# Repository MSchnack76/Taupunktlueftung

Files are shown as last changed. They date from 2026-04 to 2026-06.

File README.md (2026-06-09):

> [!WARNING] 
> Repository umgezogen auf die Codeberg-Plattform! Neue Versionen unter [Taupunktlueftung bei Coderberg](https://codeberg.org/MSchnack76/Taupunktlueftung.git)

# Taupunktlüftung
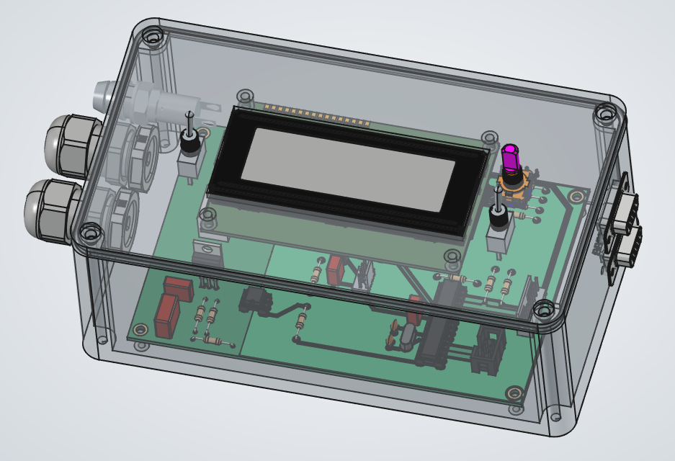
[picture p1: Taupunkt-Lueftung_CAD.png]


## Überblick
Realisierung einer Taupunkt gesteuerten Lüftung, die die Lüftung nur dann einschaltet, wenn die Taupunkt-Temperatur der Umgebungsluft (Abluftraum - bspw. außerhalb des Gebäudes) deutlich niedriger ist, als die Taupunkt-Temperatur des Raumes, der be- bzw. entlüftet werden soll.

## Elektrotechnischer Hinweis & DISCLAIMER
Ich mache an dieser Stelle darauf aufmerksam, dass diese Steuerung an einer 230V/50Hz Netzspannung betrieben wird. Es sind die einschlägigen Vorschriften für das Arbeiten, Anschließen und Betreiben einer elektrischen Anlage an 230V/50Hz zu beachten! Personen, die weder Erfahrung noch die nötige Ausbildung in der Elektrotechnik besitzen rate ich daher ausdrücklich vom Nachbau ab.
Dies ist ein Hobby-Projekt mit keinerlei Zualssung für den regelmäßigen Betrieb / Anschluss am 230V/50Hz Netz.

Alle Daten und Dateien sind nach bestem Wissen und Gewissen erstellt, haben jedoch PROTOTYPEN-Status!
Daher übernehme ich keinerlei Verantwortung für die Korrektheit der Daten und keinerlei Verantwortung für irgendwelche Schäden, die aus einem evt. Nachbau resultieren!
Diese Dokumentation ist ein rein privates Versuchs-Objekt!

## Umsetzung
### Elektronik & Leiterplatte (PCB)
Für die Steuerung kommt ein Microcontroller vom Typ Atmel 328P zum Einsatz. Der Lüfter wird über einen Optokoppler MOC3021M / TRIAC BTA 16-600 angesteuert, die mit Peripherie-Beschaltung ein Solid-State-Relais bilden.
Die Messung der Temperaturen und relativen Luftfeuchten des Abluftraumes / zu belüftenden Raumes wird über Sensoren vom Typ GY-21 HTU21 realisiert, die über einen I²C-Multiplexer TCA9543ADR an den Microcontroller angebunden werden.

Eine Daten-Ausgabe findet auf einem LCD-Display (DOT-Matrix) mit 4 Zeilen zu je 20 Zeichen (4x20) statt, welches über I²C an den Microcontroller angebunden wird. Die Hintergrundbeleuchtung des Displays kann über einen Kipptaster aktiviert werden. Der gleiche Kipptaster löst in der anderen Richtung einen Reset des Mikrocontrollers aus.

Ein Dreh-Encoder mit Tast-Funktion wird für die Menu-Steuerung eingesetzt. Das Menu und die Einstellungen werden über das LCD-Display angezeigt. Folgende Parameter können über das Menu verändert und entsprechend gesetzt werden:
a) Delta Taupunkt Schaltschwelle für das Einschalten des Lüfters (Minimales Delta zwischen Taupunkt innen und außen)
   --> Vorgabewert 5°C
b) Hystere Delta Taupunkt für das Abschalten des Lüfters
   --> Vorgabewert 1°C
c) Minimale Innenraum-Temperatur (unterhalb der Temperatur findet keine Lüftung statt)
   --> Vorgabewert 3°C
d) Minimale Außen-Temperatur (unterhalb der Temperatur findet keine Lüftung statt)
   --> Vorgabewert -10°C

Über einen Kipp-Schalter kann die Steuerung in den
1. dauerhaft EIN-Modus (Lüfter läuft ständig)
2. deaktivierten Modus (Lüfter ist dauerhaft deaktiviert)
3. in den Automatik-Modus (Taupunkt gesteuerte Be- bzw. Entlüftung)
versetzt werden.

Die Leiterplatte ist für eine Stromaufnahme von 5A bei 230VAC ausgelegt und wird über eine entsprechende Sicherung 5x20mm, 5A mittelträge vor Überstrom geschützt. Der Kleinspannungsbereich auf der PCB ist zusätzlich über eine Sicherung 5x20mm, 500mA flink abgesichert.

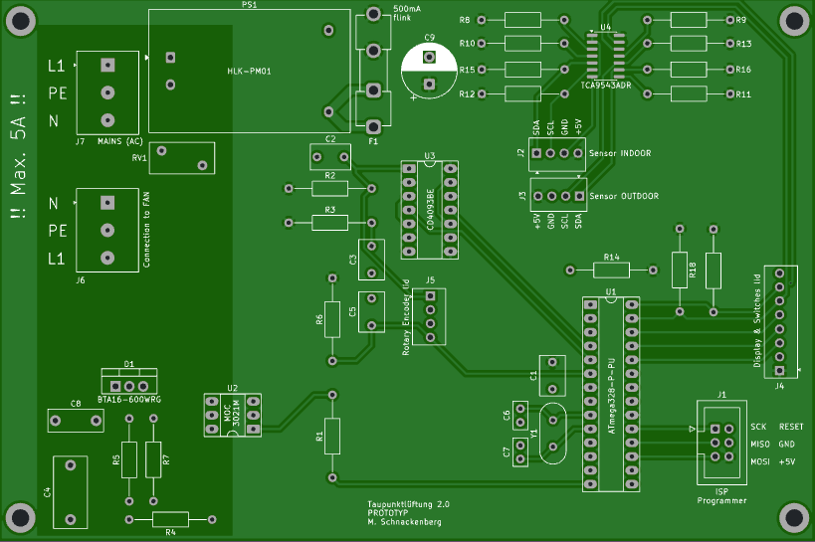
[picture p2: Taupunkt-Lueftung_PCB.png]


Der Aufbau findet bewusst im aktuellen Stadium der Entwicklung mit THT-Bauteilen (mit Ausnhame des I²C-Multiplexers, den es nur als SMD SO-14 Package gibt) statt.

### Gehäuse
Das Gehäuse wurde über eine CAD-Software konstruiert und mittels 3D-Druck erstellt. Alle Komponenten wurden im 3D-Modell eingefügt.
Die Leiterplatte sitzt auf Distanzbolzen des Gehäuses, das Display ist an der Rückseite des Deckels befestigt. Die Konnektivität der Sensoren ist über D-SUB Buchsen / Stecker realisiert.

### Verwendete Software
|Programm |Verwendung |Dateiformat |
|---|---|---|
| [FreeCAD](https://www.freecad.org) | CAD Konstruktionen | .FCStd |
| 3D-Druck | Standard Tessellation Language | .stl |
| [KiCAD](https://www.kicad.org/)| Schaltpläne | .kicad_sch |
| [KiCAD](https://www.kicad.org/)| PCB Layout | .kicad_pcb |
| [KiCAD](https://www.kicad.org/)| Projekt | .kicad_pro |
| [VisualStudioCode](https://code.visualstudio.com/)| Programmcode | .h und .cpp |
| [PlatformIO](https://platformio.org/)| Programmcode | .h und .cpp |
| [LibreOffice](https://www.libreoffice.org/)| Stückliste | .ods |

### PCB Hersteller
Ich bin sehr zufrieden mit dem deutschen PCB-Hersteller AISLER Germany GmbH mit Sitz in Aachen.

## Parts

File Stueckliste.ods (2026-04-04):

Referenz | # | Wert | Hersteller | MPN | Beschreibung
C1,C2,C3,C5 | 4 | 100n | Wima | MKS2C031001A00KSSD | MKS2 PET-Kondensator, 100 nF, 10 %, 63 VDC, RM 5
C4 | 1 | 47nF | Wima | MKP1G024703G00KSSD | 47nF 400V 10%
C6,C7 | 2 | 22p |  |  | Miniatur Scheibenkondensator, 22pF, 100V, RM 2,5mm
C8 | 1 | 10nF | Wima | MKP1G021002C00KSSD | 10nF 400V 10% Metal Film Capacitor
C9 | 1 | 1000µF/16V | Panasonic | EEUFC1C102 | Polarized capacitor 1000 µF, 16 VDC,
D1 | 1 | BTA16-600SWRG | ST | BTA16-600SWRG | TRIAC 600V 16A, TO-220AB
F1 | 1 | 500mA | ESKA | 520614 | Sicherung, 5x20mm, 500mA, flink
J1 | 1 | Wannenstecker, 6-polig, 2-reihig | Würth Electronic | 61200621621 | CONN HEADER VERT 6POS 2.54MM, 2 rows
J2, J3, J5 | 3 | Stiftleiste, 4-polig, Kodierung | binder mpe GmbH | 428-1-004-0-T-KS0 | Stiftleiste mit Kodierung und Verrastung 2,54 mm Serie 428, 4-polig
J4 | 1 | Stiftleiste, 8-polig, Kodierung | binder mpe GmbH | 428-1-008-0-T-KS0 | Stiftleiste mit Kodierung und Verrastung 2,54 mm Serie 428, 8-polig
J6, J7 | 1 | Schraubklemme, 3-polig | Metz Connect | 31073103 | Metz Connect RT026xxHBLU (Typ 073), 3-polig
J8 | 1 | Kupplungsgehäuse, 8-polig | MPE Garry GmbH | 431-1-008-X-KS0 | Kupplung, Crimptechnik, 8-polig, Leergehäuse
J9, J10, J11 | 3 | Kupplungsgehäuse, 4-polig | MPE Garry GmbH | 431-1-004-X-KS0 | Kupplung, Crimptechnik, 4-polig, Leergehäuse
 | 20 | Crimpkontakte | MPE Garry GmbH | 611-1-TX-XR | Crimpkontakte für PSK Kupplungsgehäuse
PS1 | 1 | HLK-PM01 | Shenzhen Hi-Link Electronic Co., Ltd. | HLK-PM01 | Compact AC/DC board mount power module 3W 5V
R1,R4 | 2 | 360 Ohm | YAGEO | CFR-25JT-52-360R | Kohleschicht, 360 Ohm, 5%, 250 mW, 250 VDC
R2,R3,R6 | 3 | 100 kOhm | Yageo | CFR-25JT-52-100K | Kohleschicht, 100 kOhm, 5%, 250 mW, 250 VDC
R5 | 1 | 470 Ohm | Yageo | CFR-25JT-52-470R | Kohleschicht, 470 Ohm, 5%, 250 mW, 250 VDC
R7 | 1 | 39 Ohm | VISHAY | MBB02070C3909FCT00 | 39Ω 600mW 350V Thin Film Resistor ±1%
R8,R9,R10, R11,R14 | 5 | 10k | Yageo | CFR-25JT-52-10K | Kohleschicht, 10 kOhm, 5%, 250 mW, 250 VDC
R12,R13,R15, R16,R17,R18 | 6 | 4,7 kOhm | Yageo | CFR-25JT-52-4K7 | Kohleschicht, 4,7 kOhm, 5%, 250 mW, 250 VDC
RV1 | 1 | ERZV10D391 | Panasonic | ERZV10D391 | Voltage dependent resistor 250VAC, 10%
SW1 | 1 | EC11B09 | ALPS | 401755 | Rotary encoder, dual channel, Incremental quadrate outputs, with switch
SW2 | 1 | Kippschalter, Mitte aus, 1-polig | MIYAMA | MS 500 C-B | Switch, single pole double throw, center OFF position
SW3 | 1 | Kipptaster, Mitte aus, 1-polig | MIYAMA | MS 500 E | Switch, single pole double throw, center OFF position
U1 | 1 | ATmega328-P-PU | Microchip | ATMEGA328P-PU | 20MHz, 32kB Flash, 2kB SRAM, 1kB EEPROM, DIP-28
U2 | 1 | MOC3021M | ONSEMI | MOC3021M | Random Phase Opto-Triac, Vdrm 400V, Ift 15mA, DIP6
U3 | 1 | CD4093BE | Texas Instruments | CD4093BE | CMOS Quad 2-Input NAND Schmitt Trigger
U4 | 1 | TCA9543ADR | Texas Instruments | TCA9543ADR | Low Voltage 2-Channel I2C Bus Switch
U5 | 1 | COM-LCD20X4 | Joy-IT | COM-LCD20X4 | LCD 20x4 Alphanumeric 16pin Backlight, 8bit parallel, 3.3V VDD
U6 | 1 | I2C Disp_Interface |  |  | 8-bit I/O Expander, I2C interface Module
Y1 | 1 | HC49/4H 16MHz | Würth Electronic | 830058383B | Frequenz 16,0000 MHz Frequenztoleranz 30 ppm
Sockel U1 | 1 | IC-Sockel, 28-polig | TE Connectivity | 2485264-7 | IC-Sockel, 28-polig, superflach, gedreht, schmal
Sockel U2 | 1 | IC-Sockel, 6-polig | TE Connectivity | 2485267-1 | IC-Sockel, 6-polig, superflach, gedreht, schmal
Sockel U3 | 1 | IC-Sockel, 14-polig | TE Connectivity | 2485264-2 | IC-Sockel, 14-polig, superflach, gedreht, schmal
U7, U8 | 2 | GY-21 |  |  | GY-21 Temperatur & Luftfeuchte Sensor-Modul basierend auf HTU21D
F2 | 1 | Feinsicherung 5A | ESKA | 521.024 | Sicherung, 5x20mm, 5A, mittelträge
Halter F1 | 2 | Sicherungshalter F1 | Eaton | BK/1A5601-01 | Sicherungshalter Print 5x20
Drehknopf SW1 | 1 | Kunststoffdrehknopf | CLIFF Electronic Components Ltd | CL178883 | Kunststoff-Drehknopf, schwarz, 6mm
Kappe Drehknopf SW1 | 1 | Kappe Kunststoffdrehknopf | CLIFF Electronic Components Ltd | CL1730 | Kappe für Drehknopf
J12, J13 | 2 | D-Sub 9-pol Buchse, Einbau | Encitech Connectors AB | 2101-0180-11 | D-SUB Buchse, Einbau, 9-polig, Lötkelche
J14, J15 | 2 | D-Sub 9-pol Steckverbinder | MH Connectors | MHDTZK9-DB9P-K | D-SUB Stecker, 9-polig Zweiteil. Backshell Steckverbinder
Halter F2 | 1 | Sicherungshalter F2 | SCHURTER | 3101.0015 | Sicherungshalter für 5 x 20 mm, 250 V, 10 A, schwarz
 | 1 | Leiterplatte Taupunkt-Lüftung Rev.2 | AISLER Germany GmbH |  | Leiterplatte nach Design
 | 8 | M3x10mm Selbstschneid. Schraube |  |  | Leiterplatten & Display Verschraubung
 | 4 | M4x12mm Selbstschneid. Schraube |  |  | Deckel Verschraubung auf Gehäuse
 | 4 | Distanzbolzen, 6-Kant, M3, 5mm | VOGT AG | DA5M3X05 | Verschraubung D-SUB Buchse in Gehäuse
 | 4 | Mutter, M3 |  |  | Verschraubung D-SUB Buchse in Gehäuse
 | 2 | Gegenmutter PG11 | LAPP | 53019020 | Für Zuleitungs- und Ventilator-Leitungs-Einlass
 | 2 | Verschraubung PG11 | LAPP | 53015020 | Für Zuleitungs- und Ventilator-Leitungs-Einlass
 | 1 | Gehäuse mit Deckel |  |  | nach CAD-Zeichnung, 3D-Druck
 |  | Fernmeldeleitung 2x2x0,6 |  |  | für Temperatur-Sensor-Leitung, Länge wie benötigt

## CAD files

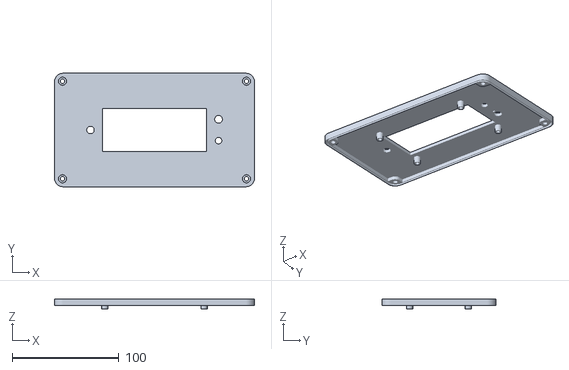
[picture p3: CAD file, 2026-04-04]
Taupunkt_Lueftung_Gehaeuse-Deckel.stl
187.4 x 106.4 x 9.00

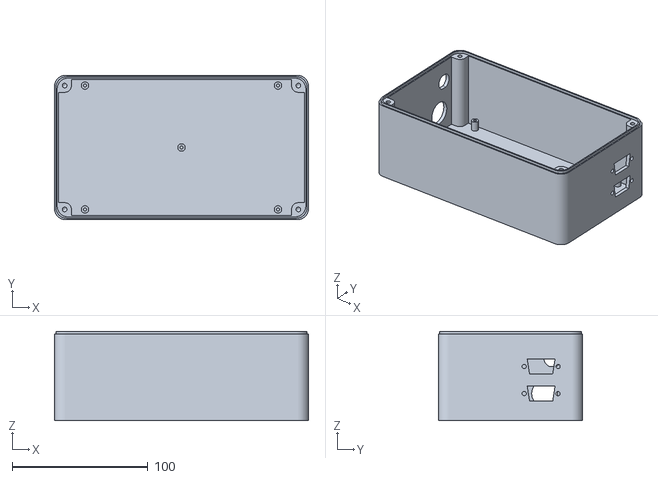
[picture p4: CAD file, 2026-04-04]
Taupunkt_Lueftung_Gehaeuse-Unterteil.stl
187.4 x 106.4 x 66.0

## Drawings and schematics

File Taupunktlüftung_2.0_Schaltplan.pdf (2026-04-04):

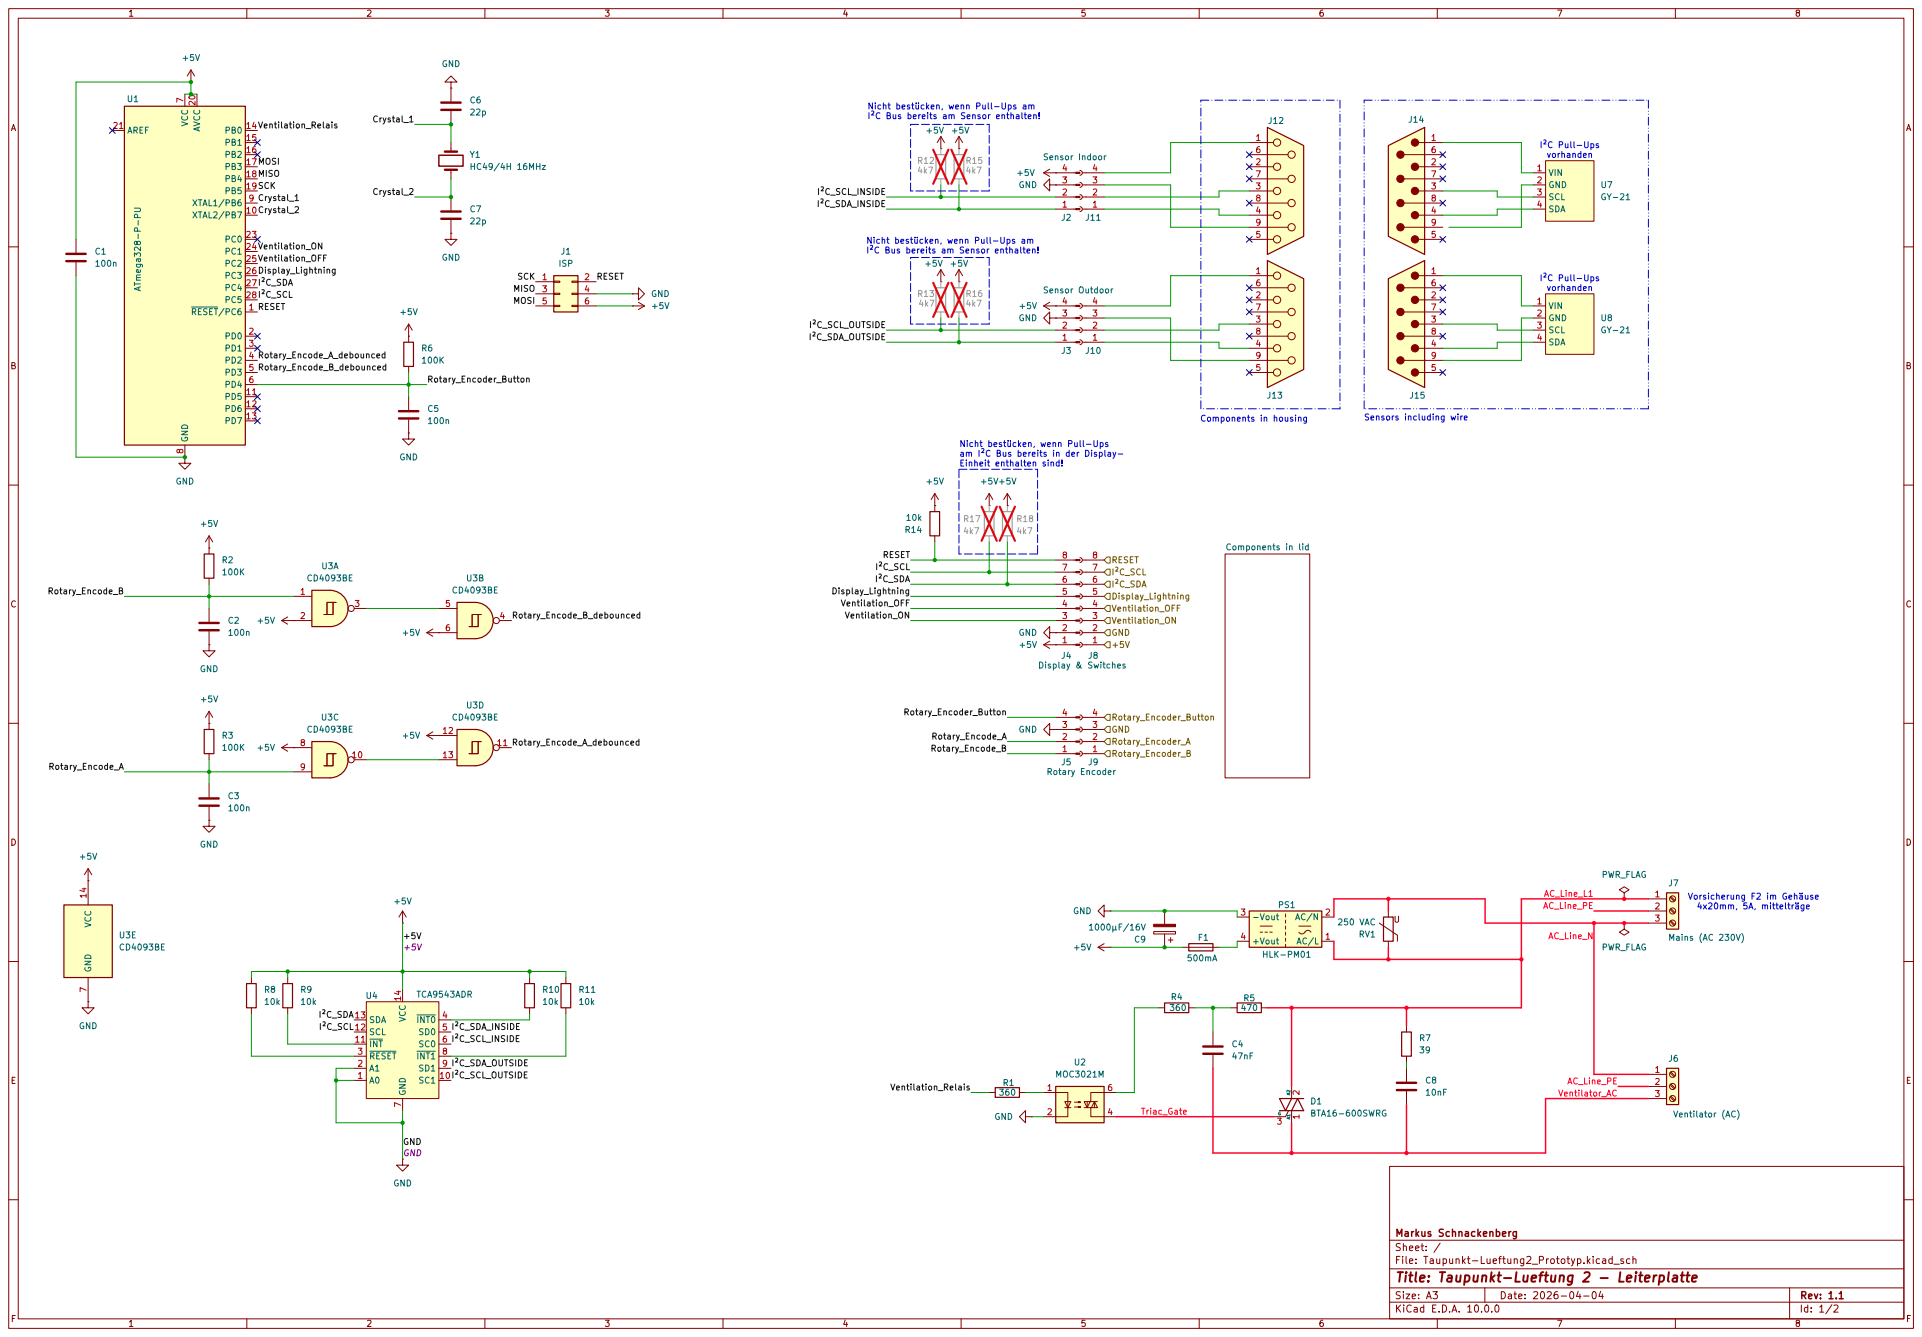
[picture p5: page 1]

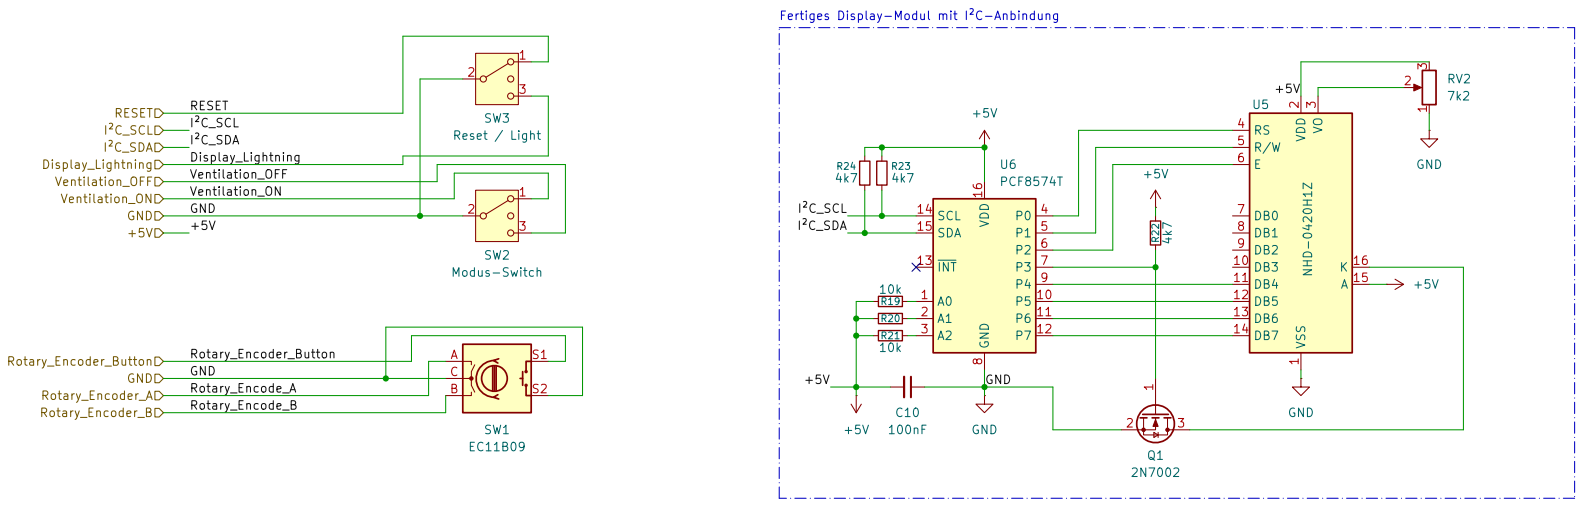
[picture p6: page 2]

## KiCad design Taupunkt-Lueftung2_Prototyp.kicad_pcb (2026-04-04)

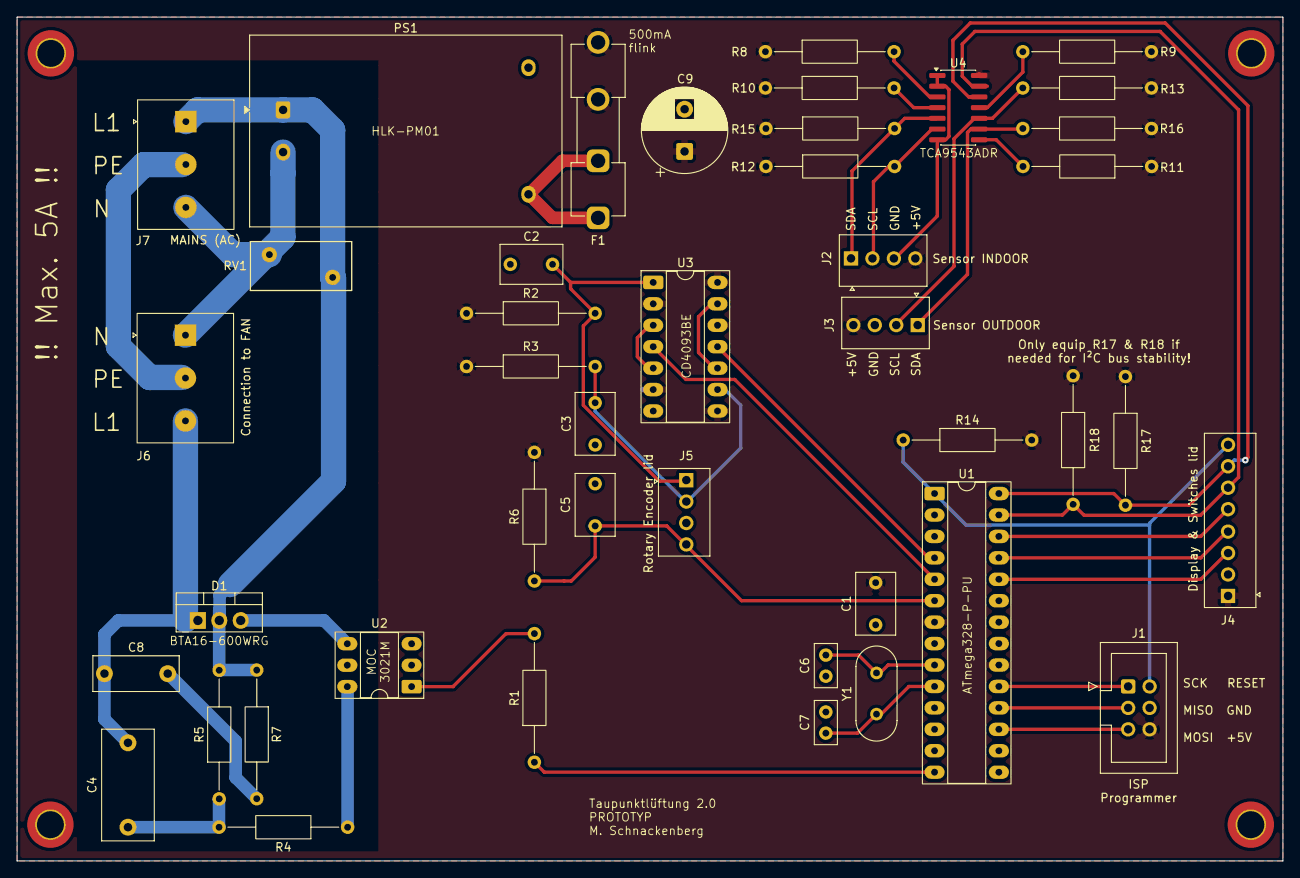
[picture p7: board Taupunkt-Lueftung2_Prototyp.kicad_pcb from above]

Board: 2 copper layers, 150.0 x 100.0 mm, 43 parts (0 on the bottom side), 39 nets.

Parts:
C1, C2, C3, C5: 100n; C_Rect_L7.2mm_W4.5mm_P5.00mm_FKS2_FKP2_MKS2_MKP2
C4: 47nF; C_Rect_L13.0mm_W6.0mm_P10.00mm_FKS3_FKP3_MKS4
C6, C7: 22p; C_Disc_D5.0mm_W2.5mm_P2.50mm
C8: 10nF; C_Rect_L10.0mm_W4.0mm_P7.50mm_FKS3_FKP3
C9: 1000µF/16V; CP_Radial_D10.0mm_P5.00mm
D1: BTA16-600SWRG; TO-220-3_Vertical
F1: 500mA; Fuseholder_Clip-5x20mm_Eaton_1A5601-01_Inline_P20.80x6.76mm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
J1: ISP; IDC-Header_2x03_P2.54mm_Vertical
J2: Sensor Indoor; Connector_Encoding_4x1_MPE_428-1-004-0-T-KS0
J3: Sensor Outdoor; Connector_Encoding_4x1_MPE_428-1-004-0-T-KS0
J4: Display & Switches; Connector_Encoding_8x1_MPE_428-1-008-0-T-KS0
J5: Rotary Encoder; Connector_Encoding_4x1_MPE_428-1-004-0-T-KS0
J6: Ventilator (AC); Connector_Screwterminal_3x1_MetzConnect_31073103
J7: Mains (AC 230V); Connector_Screwterminal_3x1_MetzConnect_31073103
PS1: HLK-PM01; Converter_ACDC_Hi-Link_HLK-PMxx
R1, R4: 360; R_Axial_DIN0207_L6.3mm_D2.5mm_P15.24mm_Horizontal
R2, R3, R6: 100K; R_Axial_DIN0207_L6.3mm_D2.5mm_P15.24mm_Horizontal
R5: 470; R_Axial_DIN0207_L6.3mm_D2.5mm_P15.24mm_Horizontal
R7: 39; R_Axial_DIN0207_L6.3mm_D2.5mm_P15.24mm_Horizontal
R8, R9, R10, R11, R14: 10k; R_Axial_DIN0207_L6.3mm_D2.5mm_P15.24mm_Horizontal
R12, R13, R15, R16, R17, R18: 4k7; R_Axial_DIN0207_L6.3mm_D2.5mm_P15.24mm_Horizontal
RV1: 250 VAC; RV_Disc_D12mm_W5.8mm_P7.5mm
U1: ATmega328-P-PU; DIP-28_W7.62mm_Socket_LongPads
U2: MOC3021M; DIP-6_W7.62mm_Socket_LongPads
U3: CD4093BE; DIP-14_W7.62mm_Socket_LongPads
U4: TCA9543ADR; SOIC-14_3.9x8.7mm_P1.27mm
Y1: HC49/4H 16MHz; Crystal_HC49-4H_Vertical

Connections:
+5V: C1.1, C9.1, F1.2, J1.6, J2.4, J3.4, J4.1, R2.1, R3.1, R6.1, R8.1, R9.1, R10.1, R11.1, R12.1, R13.1, R14.2, R15.1, R16.1, R17.1, R18.1, U1.7 (VCC), U1.20 (AVCC), U3.2, U3.6, U3.8, U3.12, U3.14 (VCC), U4.14 (VCC)
/AC_Line_L1: D1.2 (A2), J7.1, PS1.1 (AC/L), R5.2, R7.1, RV1.1
/AC_Line_N: J6.1, J7.3, PS1.2 (AC/N), RV1.2
/AC_Line_PE: J6.2, J7.2
/Crystal_1: C6.2, U1.9 (XTAL1/PB6), Y1.2
/Crystal_2: C7.1, U1.10 (XTAL2/PB7), Y1.1
/Display_Lightning: J4.5, U1.26 (PC3)
/I²C_SCL: J4.7, R17.2, U1.28 (PC5), U4.12 (SCL)
/I²C_SCL_INSIDE: J2.2, R12.2, U4.6 (SC0)
/I²C_SCL_OUTSIDE: J3.2, R13.2, U4.10 (SC1)
/I²C_SDA: J4.6, R18.2, U1.27 (PC4), U4.13 (SDA)
/I²C_SDA_INSIDE: J2.1, R15.2, U4.5 (SD0)
/I²C_SDA_OUTSIDE: J3.1, R16.2, U4.9 (SD1)
/MISO: J1.3, U1.18 (PB4)
/MOSI: J1.5, U1.17 (PB3)
/RESET: J1.2, J4.8, R14.1, U1.1 (~RESET/PC6)
/Rotary_Encode_A: C3.1, J5.2, R3.2, U3.9
/Rotary_Encode_A_debounced: U1.4 (PD2), U3.11
/Rotary_Encode_B: C2.1, J5.1, R2.2, U3.1
/Rotary_Encode_B_debounced: U1.5 (PD3), U3.4
/Rotary_Encoder_Button: C5.1, J5.4, R6.2, U1.6 (PD4)
/SCK: J1.1, U1.19 (PB5)
/Triac_Gate: D1.3 (G), U2.4
/Ventilation_OFF: J4.4, U1.25 (PC2)
/Ventilation_ON: J4.3, U1.24 (PC1)
/Ventilation_Relais: R1.1, U1.14 (PB0)
/Ventilator_AC: C4.2, C8.2, D1.1 (A1), J6.3
GND: C1.2, C2.2, C3.2, C5.2, C6.1, C7.2, C9.2, J1.4, J2.3, J3.3, J4.2, J5.3, PS1.3 (-Vout), U1.8 (GND), U1.22 (GND), U2.2, U3.7 (GND), U4.1 (A0), U4.2 (A1), U4.7 (GND)
unnamed: C4.1, R4.2, R5.1
unnamed: C8.1, R7.2
unnamed: F1.1, PS1.4 (+Vout)
unnamed: R1.2, U2.1
unnamed: R4.1, U2.6
unnamed: U3.3, U3.5
unnamed: U3.10, U3.13
unnamed: R10.2, U4.4 (~INT0)
unnamed: R11.2, U4.8 (~INT1)
unnamed: R9.2, U4.11 (~INT)
unnamed: R8.2, U4.3 (~RESET)

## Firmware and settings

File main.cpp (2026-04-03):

/*
Taupunkt-Luefter-Steuerung Version 2.0
2026-03-29 Markus Schnackenberg

In Version 2.0 Ergänzung um Inkremental-Geber (Dreh-Encoder) mit Menu-Steuerung zur Einstellung der Schaltpunkte (Delta-Tauwert zur Einschaltung des Lüfters,
Hysteres zum Ausschaltenm des Lüfters, minimale Innen- und Außen-Temperatur für eine Belüftung). Die Schaltpunkte werden auf initiale-Werte gesetzt, im
internen EEPROM des Mikrocontrollers gespeichert und können dort entsprechend über das Menu verändert und dauerhaft gespeichert werden.
Der Betrieb der Tau-Punkt-Lüftung ist auch ohne den Dreh-Encoder möglich (mit den initialen Werten für die Schaltpunkte).

Sensoren: GY-21 (Temperatur und Luftfeuchte) angebunden über PCA9548A I2C-Multiplexer
          Multiplexer notwendig, da die verwendeten Sensoren GY-21 eine feste I2C-Adresse 0x40
          verwenden und die Adresse nicht 2-fach auf dem I2C-Bus existieren kann
Display:  LCD-DOT-Matrix, HD44780 kompatibel, 4x20 Zeichen mit I2C-Anbindung
*/

#include "functions.h"            // Projekt-Datei - Auslagerung von globalen Variablen, Funktionen und Bilbliothek-Einbindungen

void setup()
{
  wdt_enable(WDTO_8S);                 // Watchdog timer auf 8 Sekunden stellen
  pinMode(RELAISPIN, OUTPUT);          // Relaispin als Output definieren
  digitalWrite(RELAISPIN, RELAIS_AUS); // Relais und damit den Lüfter ausschalten
  pinMode(MAN_AUS, INPUT_PULLUP);      // Pin für Lüfter manuell aus als Input definieren (mit internem PullUp-Widerstand)
  pinMode(MAN_EIN, INPUT_PULLUP);      // Pin für Lüfter manuell ein als Input definieren (mit internem PullUp-Widerstand)
  pinMode(LICHT, INPUT_PULLUP);        // Pin für Display-Beleuchtungs-Taster als Input definieren (mit internem PullUp-Widerstand)
  pinMode(MENUBUTTON, INPUT_PULLUP);   // Pin vom Dreh-Encoder Taster zum Aufruf des Menu & Eingabe-Bestätigungen im Menu (mit internem PullUp-Widerstand)
  pinMode(ENCODER_A, INPUT_PULLUP);    // Pin A vom Dreh-Encoder, entprelltes Signal über Schmitt-Trigger Inverter & Inverter (CD4093BE)
  pinMode(ENCODER_B, INPUT_PULLUP);    // Pin B vom Dreh-Encoder, entprelltes Signal über Schmitt-Trigger Inverter & Inverter (CD4093BE)
  state=INIT;                          // State Machine auf Status INIT setzen
  
  lcd.init();                     // LCD-Display initialisieren
  lcd.backlight();                // LCD-Display Belechtung einschalten

  I2C_multiplexer_channel(0);     // I2C-Multiplexer Kanal 0 anwählen
  GY21_sensor_init(0x40);         // Initialisieren von Sensor 1 (Innen)
  I2C_multiplexer_channel(1);     // I2C-Multiplexer Kanal 1 anwählen
  GY21_sensor_init(0x40);         // Initialisieren von Sensor 2 (Aussen)

  attachInterrupt(digitalPinToInterrupt(ENCODER_B), encoder_interrupt, CHANGE);

  
  byte check_eeprom = EEPROM[0];  // Speichervariable für EEPROM ist leer Überprüfung
  if (check_eeprom != 0x1A)       // WENN EEPROM leer (Prüfkennzeichnung Speicheradresse 0 ist NICHT 0x1A), DANN
  {                               // >>
    EEPROM.put(0, 0x1A);          // schreibe Prüfkennzeichnung ins EEPROM (Speicheradresse 0, Wert 0x1A)
    EEPROM.put(10, SCHALTmin);    // schreibe Standard-SCHALTmin ins EEPROM (Speicheradresse 10, Wert 5.0)
    EEPROM.put(20, HYSTERESE);    // schreibe Standard-HYSTERESE ins EEPROM (Speicheradresse 20, Wert 1.0)
    EEPROM.put(30, TEMP1_min);    // schreibe Standard-Min-Temperatur innen ins EEPROM (Speicheradresse 30, Wert 3.0)
    EEPROM.put(40, TEMP2_min);    // schreibe Standard-Min-Temperatur aussen ins EEPROM (Speicheradresse 40, Wert -10.0)
  }                               // <<
  else                            // SONST
  {                               // >>
    EEPROM.get(10, SCHALTmin);    // lese EEPROM Speicheradresse 10 und schreibe den Wert in die Variable SCHALTmin
    EEPROM.get(20, HYSTERESE);    // lese EEPROM Speicheradresse 20 und schreibe den Wert in die Variable HYSTERESE
    EEPROM.get(30, TEMP1_min);    // lese EEPROM Speicheradresse 30 und schreibe den Wert in die Variable TEMP1min
    EEPROM.get(40, TEMP2_min);    // lese EEPROM Speicheradresse 30 und schreibe den Wert in die Variable TEMP2min
  }
}

void loop()
{
  char ch1[8];        // Speichervariable für Luftfeuchte Sensor 1 (Innen) - nach Wandlung in Zeichenkette für Display-Ausgabe
  char ct1[8];        // Speichervariable für Temperatur Sensor 1 (Innen) - nach Wandlung in Zeichenkette für Display-Ausgabe
  char ch2[8];        // Speichervariable für Luftfeuchte Sensor 2 (Aussen) - nach Wandlung in Zeichenkette für Display-Ausgabe
  char ct2[8];        // Speichervariable für Temperatur Sensor 2 (Aussen) - nach Wandlung in Zeichenkette für Display-Ausgabe
  char cdp1[8];       // Speichervariable für errechneten Taupunkt Innen - nach Wandlung in Zeichenkette für Display-Ausgabe
  char cdp2[8];       // Speichervariable für errechneten Taupunkt Aussen - nach Wandlung in Zeichenkette für Display-Ausgabe
  char cDeltaTP[8];   // Speichervariable für errechneten Delta-Taupunkt zwischen Innen und Aussen - nach Wandlung in Zeichenkette für Display-Ausgabe
  char cSCHALTmin[8]; // Speichervariable für Delta-Taupunkt Schaltschwelle Lüfter ein - nach Wandlung in Zeichenkette für Display-Ausgabe
  char cHYSTERESE[8]; // Speichervariable für Hysterese Schaltschwelle Lüfter aus - nach Wandlung in Zeichenkette für Display-Ausgabe
  char cTEMP1min[8];  // Speichervariable für minimale Innen-Temperatur Belüftung - nach Wandlung in Zeichenkette für Display-Ausgabe
  char cTEMP2min[8];  // Speichervariable für minimale Aussen-Temperatur Belüftung - nach Wandlung in Zeichenkette für Display-Ausgabe

  display_light(LICHT);                                     // Display-Hintergrundbeleuchtung steuern über Funktionsbaustein
  write_to_display(display0, display1, display2, display3); // Display-Ausgabe schreiben über Funktionsbaustein (Übergabe der Inhalte der 4 Zeilen)

  if ((digitalRead(MENUBUTTON) == LOW) && (state != MENU))  // WENN Encoder-Button gedrückt UND State Machine nicht im Status "MENU", DANN
  {                                                         // >>
    Encoder_Position = 0;                                   // setze Encoder_Positions-Variable auf Wert 0
    state=MENU;                                             // Setze State Machine Status "MENU"
    delay(200);                                             // Verzögerungszeit für Tasten-Druck Encoder-Taste (kein versehentliches "Springen" ins Menu)
  }                                                         // <<

  if (state == SENSOR_FEHLER)                       // WENN State Machine im Status "Sensor Fehler", DANN
  {                                                 // >>
    state=DATEN;                                    // Setze State Machine Status "DATEN"
  }                                                 // <<

  I2C_multiplexer_channel(0);                       // I2C-Multiplexer Kanal 0 anwählen (Sensor Innen)
  double h1 = GY21_read_humidity(0x40);             // Luftfeuchte Sensor 1 (Innen) auslesen und in "h1" speichern 
  double t1 = GY21_read_temperature(0x40);          // Temperatur Sensor 1 (Innen) auslesen und in "t1" speichern
  float dp1 = calculate_dewpoint(t1, h1);           // Taupunkt-Temperatur Innen errechnen und in "dp1" speichern
  
  if (h1 < 0)                                       // WENN Luftfeuchte Sensor 1 (Innen) in "h1" kleiner als 0, DANN
  {                                                 // >>
    state = SENSOR_FEHLER;                          // Setze State Machine Status "SENSOR_FEHLER"
    strcpy( display2, "  SENSOR 1 innen    " );     // Setze Display-Zeile 3 auf "SENSOR 1 innen"
  }                                                 // <<
  else if (state != INIT)                           // WENN SONST State Machine nicht im Status "INIT"
  {                                                 // >>
    strcpy( display2, "                    " );     // Setze Display-Zeile 3 auf leer
  }                                                 // <<

  I2C_multiplexer_channel(1);                       // I2C-Multiplexer Kanal 1 anwählen (Sensor Aussen)
  double h2 = GY21_read_humidity(0x40);             // Luftfeuchte Sensor 2 (Aussen) auslesen und in "h2" speichern
  double t2 = GY21_read_temperature(0x40);          // Temperatur Sensor 2 (Aussen) auslesen und in "t2" speichern
  float dp2 = calculate_dewpoint(t2, h2);           // Taupunkt-Temperatur Aussen errechnen und in "dp2" speichern

  if (h2 < 0)                                       // WENN Luftfeuchte Sensor 2 (Aussen) in "h2" kleiner als 0, DANN
  {                                                 // >>
    state = SENSOR_FEHLER;                          // Setze State Machine Status "SENSOR_FEHLER"
    strcpy( display3, "  SENSOR 2 aussen   " );     // Setze Inhalt von Display-Variable Zeile 4 auf "SENSOR 2 aussen"
  }                                                 // <<
  else if (state != INIT)                           // WENN SONST State Machine nicht im Status "INIT"
  {                                                 // >>
    strcpy( display3, "                    " );     // Setze Inhalt von Display-Variable Zeile 4 auf leer
  }                                                 // <<

  float DeltaTP = dp1 - dp2;                        // Delta-Taupunkt von Innen zu Aussen berechnen und in "DeltaTP" speichern

  static unsigned long lastexec = 0;                // Einmalige Initialisierung der Variable "lastexec" für Zeitstempel letzte Ausführung
  unsigned long timepassed = millis() - lastexec;   // Vergangene Zeit seit letzer Ausführung errechnen und in "timepassed" speichern

  switch (state)                                    /* --> State Machine - Fall Auswertung <-- */
  {
    case INIT:                                      // >>>> State Machine IST im Status "INIT"
      digitalWrite(RELAISPIN, RELAIS_EIN);          // Lüfter über Relais einschalten (Lüfter-Test)
      if (timepassed > 1000)                        // WENN State Machine länger als 7 Sekunden im Status "INIT"
      {                                             // >>
        dtostrf(SCHALTmin, 5, 1, cSCHALTmin);       // Wandle SCHALTmin-Wert in Zeichenkette und speichere in Variable "cSCHALTmin"
        dtostrf(HYSTERESE, 5, 1, cHYSTERESE);       // Wandle HYSTERESE-Wert in Zeichenkette und speichere in Variable "cHYSTERES"
        dtostrf(TEMP1_min, 5, 1, cTEMP1min);        // Wandle TEMP1min-Wert (minimnale Innen-Temperatur) in Zeichenkette und speichere in Variable "cTEMP1min"
        dtostrf(TEMP2_min, 5, 1, cTEMP2min);        // Wandle TEMP2min-Wert (minimnale Aussen-Temperatur) in Zeichenkette und speichere in Variable "cTEMP2min"
        strcpy( display0, "TauSchalt : " );         // Setze Inhalt von Display-Variable Zeile 1
        strcat( display0, cSCHALTmin );             // Hänge Zeichenkette für minimale Delta-Taupunkt-Schalt-Temperatur an Display-Variable 1
        strcat( display0, "C  " );                  // Hänge "C  " an Display-Variable 1 an
        strcpy( display1, "Hysterese : " );         // Setze Inhalt von Display-Variable Zeile 2
        strcat( display1, cHYSTERESE );             // Hänge Zeichenkette für Hysterese an Display-Variable 2
        strcat( display1, "C  " );                  // Hänge "C  " an Display-Variable 2 an
        strcpy( display2, "TempInMin : " );         // Setze Inhalt von Display-Variable Zeile 3
        strcat( display2, cTEMP1min );              // Hänge Zeichenkette für minimale Temperatur innen an Display-Variable 3
        strcat( display2, "C  " );                  // Hänge "C  " an Display-Variable 3 an
        strcpy( display3, "TempOutMin: " );         // Setze Inhalt von Display-Variable Zeile 4
        strcat( display3, cTEMP2min );              // Hänge Zeichenkette für minimale Temperatur aussen an Display-Variable 4
        strcat( display3, "C  " );                  // Hänge "C  " an Display-Variable 4 an
        digitalWrite(RELAISPIN, RELAIS_AUS);        // Lüfter über Relais ausschalten (Ende Lüfter-Test)
      }                                             // <<
      if (timepassed > 5000)                        // WENN State Machine länger als 14 Sekunden im Status "INIT", DANN
      {                                             // >>
        lastexec = millis();                        // Setze letzte Ausführung über Variable "lastexec" auf aktuelle Laufzeit
        state=DATEN;                                // State Machine auf Status "DATEN"
      }                                             // <<
      wdt_reset();                                  // Watchdog zurücksetzen
      break;                                        // <<<< Switch case INIT Ende

    case EIN:                                       // >>>> State Maschine IST im Status "EIN"
      digitalWrite(RELAISPIN, RELAIS_EIN);          // Schalte Lüfter über Relais ein
      strcpy( display0, "Luefter manuell  EIN" );   // Setze Inhalt von Display-Variable Zeile 1
      strcpy( display1, "Temperatur- und Tau-" );   // Setze Inhalt von Display-Variable Zeile 2
      strcpy( display2, "punkt-Steuerung sind" );   // Setze Inhalt von Display-Variable Zeile 3
      strcpy( display3, "deaktiviert!        " );   // Setze Inhalt von Display-Variable Zeile 4
      if (timepassed > 7000)                        // WENN State Machine länger als 7 Sekunden im Status "EIN"
      {                                             // >>
        lastexec = millis();                        // Setze letzte Ausführung über Variable "lastexec" auf aktuelle Laufzeit
        state=DATEN;                                // State Machine auf Status "DATEN" setzen
      }                                             // <<
      wdt_reset();                                  // Watchdog zurücksetzen
      break;                                        // <<<< Switch case EIN Ende

    case AUTO:                                                                                  // >>>> State Maschine IST im Status "AUTO"
      dtostrf(DeltaTP, 5, 1, cDeltaTP);                                                         // DeltaTaupunkt-Wert in Zeichenkette umwandeln und in "cDeltaTP" speichern
      if ((DeltaTP > (SCHALTmin)) && (t1 > (TEMP1_min)) && (t2 > (TEMP2_min)))                  // WENN DeltaTaupunkt größer der Schaltschwelle UND Temperaturen größer den Minimal-Werten
      {                                                                                         // >>
        digitalWrite(RELAISPIN, RELAIS_EIN);                                                    // Schalte Lüfter über Relais ein
        strcpy( display1, "  Lueftung  laeuft  " );                                             // Setze Inhalt von Display-Variable Zeile 2
        strcpy( display2, "  Temperaturen  ok  " );                                             // Setze Inhalt von Display-Variable Zeile 3
      }                                                                                         // <<
      else if ((DeltaTP < (SCHALTmin - HYSTERESE)) || (t1 < (TEMP1_min)) || (t2 < (TEMP2_min))) // WENN SONST DeltaTaupunkt kleiner der Schaltschwelle minus Hysteres ODER Temperaturen kleiner den Minimal-Werten
      {                                                                                         // >>
        digitalWrite(RELAISPIN, RELAIS_AUS);                                                    // Schalte Lüfter über Relais aus
        strcpy( display1, "    Lueftung aus    " );                                             // Setze Inhalt von Display-Variable Zeile 2
        if ((t1 < (TEMP1_min)) || (t2 < (TEMP2_min)))                                           // WENN Temperaturen kleiner den Minimal-Werten
        {                                                                                       // >>>
          strcpy( display2, "Temperaturen niedrig" );                                           // Setze Inhalt von Display-Variable Zeile 3
        }                                                                                       // <<<
        else                                                                                    // SONST
        {                                                                                       // >>>
          strcpy( display2, "  Temperaturen  ok  " );                                           // Setze Inhalt von Display-Variable Zeile 3
        }                                                                                       // <<<
      }                                                                                         // <<
      strcpy( display0, "  Automatik  Modus  " );                                               // Setze Inhalt von Display-Variable Zeile 1
      strcpy( display3, "DeltaTaupunkt " );                                                     // Setze Inhalt von Display-Variable Zeile 4
      strcat( display3, cDeltaTP );                                                             // Hänge Zeichenkette für DeltaTaupunkt-Wert an Display-Variable 4
      strcat( display3, "%" );                                                                  // Hänge "%" an Display-Variable 4 an
      if (timepassed > 7000)                                                                    // WENN State Machine länger als 7 Sekunden im Status "AUTO"
      {                                                                                         // >>
        lastexec = millis();                                                                    // Setze letzte Ausführung über Variable "lastexec" auf aktuelle Laufzeit
        state=DATEN;                                                                            // State Machine auf Status "DATEN" setzen
      }                                                                                         // <<
      wdt_reset();                                                                              // Watchdog zurücksetzen
      break;                                                                                    // <<<< Switch case AUTO Ende

    case AUS:                                       // >>>> State Maschine IST im Status "AUS"
      digitalWrite(RELAISPIN, RELAIS_AUS);          // Schalte Lüfter über Relais aus
      strcpy( display0, "Luefter manuell  AUS" );   // Setze Inhalt von Display-Variable Zeile 1
      strcpy( display1, "Temperatur- und Tau-" );   // Setze Inhalt von Display-Variable Zeile 2
      strcpy( display2, "punkt-Steuerung sind" );   // Setze Inhalt von Display-Variable Zeile 3
      strcpy( display3, "deaktiviert!        " );   // Setze Inhalt von Display-Variable Zeile 4
      if (timepassed > 7000)                        // WENN State Machine länger als 7 Sekunden im Status "AUS"
      {                                             // >>
        lastexec = millis();                        // Setze letzte Ausführung über Variable "lastexec" auf aktuelle Laufzeit
        state=DATEN;                                // State Machine auf Status "DATEN" setzen
      }                                             // <<
      wdt_reset();                                  // Watchdog zurücksetzen
      break;                                        // <<<< Switch case AUS Ende

    case SENSOR_FEHLER:                                                     // >>>> State Maschine IST im Status "SENSOR_FEHLER"
      if((digitalRead(MAN_EIN) == HIGH) && (digitalRead(MAN_AUS) == HIGH))  // WENN Modus-Wahlschalter im Modus "Automatik" (Mittel-Stellung des Schalters)
      {                                                                     // >>
        digitalWrite(RELAISPIN, RELAIS_AUS);                                // Schalte Lüfter über Relais aus
      }                                                                     // <<
      strcpy( display0, "   SENSOR FEHLER    " );                           // Setze Inhalt von Display-Variable Zeile 1
      strcpy( display1, "                    " );                           // Setze Inhalt von Display-Variable Zeile 2
      wdt_reset();                                                          // Watchdog zurücksetzen
      break;                                                                // <<<< Switch case SENSOR_FEHLER Ende
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

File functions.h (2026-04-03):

#include <Arduino.h>              // Arduino Standard Bibliothek
#include <LiquidCrystal_I2C.h>    // LCD Display mit I2C Anbindung Bibliothek
#include <Wire.h>                 // Arduino I2C Bibliothek
#include <EEPROM.h>               // Arduino EEPROM Bibliothek
#include <avr/wdt.h>              // AVR Bibliothek für Watchdog

/*** Globale Variablen setzen und einmalig in main.cpp übernehmen ***/
#ifndef GLOBALS_
#define GLOBALS_

/* Definition der verwendeten Microcontroller Pins */
#define RELAISPIN 8                         // PB0, 328P Pin 14 - Luefter schalten
#define MAN_EIN 15                          // PC1, 328P Pin 24 - Schalter Ein - Auto - Aus
#define MAN_AUS 16                          // PC2, 328P Pin 25 - Schalter Ein - Auto - Aus
#define LICHT 17                            // PC3, 328P Pin 26 - Taster für LCD-Display Belechtung
#define ENCODER_A 2                         // PD2, 328P Pin 04 - Dreh-Encoder Pin A
#define ENCODER_B 3                         // PD3, 328P Pin 05 - Dreh-Encoder Pin B
#define MENUBUTTON 4                        // PD4, 328P Pin 06 - Dreh-Encoder Taster

/* Schalten des Relais über N-Feld-Effekt-Transistor, Vorwiderstand und die Masse | VCC liegt fix an der Relais-Spule an */
/* Definition der Relais-Zustände für Programmierung                                                                     */
#define RELAIS_EIN HIGH                     // Relais ein
#define RELAIS_AUS LOW                      // Relais aus

/* Definition LCD-Display */
LiquidCrystal_I2C lcd(0x27,20,4);           // LCD: I2C-Addresse und Displaygroesse setzen
char display0[21] = " Taupunkt--Lueftung "; // Speichervariable für Display Zeile 1 und Initial-Wert
char display1[21] = "    Version  2.0    "; // Speichervariable für Display Zeile 2 und Initial-Wert
char display2[21] = "    Luefter Test    "; // Speichervariable für Display Zeile 3 und Initial-Wert
char display3[21] = "Einstellungen folgen"; // Speichervariable für Display Zeile 4 und Initial-Wert

/* Definition der Konstanten für Programm-Ablauf */
double SCHALTmin = 5.0;   // minimaler Taupunktunterschied, bei dem das Relais schaltet
double HYSTERESE = 1.0;   // Abstand von Ein- und Ausschaltpunkt (Hysterese)
double TEMP1_min = 3.0;   // Minimale Innentemperatur, bei der die Lueftung aktiviert wird
double TEMP2_min = -10.0; // Minimale Außentemperatur, bei der die Lueftung aktiviert wird

/* Definition der State Machine Status */
enum { MENU, MENU1, MENU2, MENU3, MENU4, EIN, AUTO, AUS, SENSOR_FEHLER, DATEN, INIT } state;

/* Definitionen für Dreh-Encoder */
long Encoder_Position = 0;           // Variable für aktuelle Dreh-Encoder Position
long old_position = 0;               // alte Position Encoder für Menu auf/ab
int counter = 0;                     // Menu-Punkt Identifizierung

#define MULTIPLEXER_ADDR 0x70        // I2C-Adresse für PCA9548A I2C Multiplexer setzen (A0 & A1 & A2 auf Masse --> 0x70)
#define DISP_LIGHT_TIME 60000        // Dauer der Display-Hintergrund-Beleuchtung in ms

#endif


/*** FUNKTIONS-DEFINITIONEN ***/

// *** Interrupt-Routine für Dreh-Encoder ***
void encoder_interrupt()
{
  if (digitalRead (ENCODER_A) != digitalRead (ENCODER_B))
  {
    Encoder_Position++;
  }
  else
  {
    Encoder_Position--;
  }
}

// Startet das Programm neu, nicht aber die Sensoren oder das LCD
void software_Reset() 
{
  asm volatile ("  jmp 0");  
}

// *** Funktions-Definition zur Berechnung einer Taupunkt-Temperatur ***
float calculate_dewpoint(double temperature, double humidity)
{
  // Parameter für Magnus-Formel ueber/gleich und unter 0°C definieren
  float a, b;
  if (temperature >= 0)
  {
    a = 7.5;
    b = 237.3;
  }
  else if (temperature < 0)
  {
    a = 7.6;
    b = 240.7;
  }
  
  // Berechnung des Taupunktes an Hand Teamperatur und relativer Luftfeuchte
  // Sättigungsdampfdruck in hPa (Magnus-Formel)
  float sdd = 6.1078 * pow(10, (a*temperature)/(b+temperature));
  
  // Dampfdruck in hPa
  float dd = sdd * (humidity/100);
  
  // v-Parameter
  float v = log10(dd/6.1078);
  
  // Taupunkttemperatur (°C)
  float dewpoint_temperature = (b*v) / (a-v);
  return { dewpoint_temperature };  
}

// *** Definierte Zeilen auf Display ausgeben ***
void write_to_display(char *line0, char *line1, char *line2, char *line3)
{
  static unsigned long last_executed = 0;               // Einmalige Initialisierung der Variable "last_executed" für Zeitstempel letzte Ausführung
  unsigned long time_passed = millis() - last_executed; // Vergangene Zeit seit letzer Ausführung errechnen und in "time_passed" speichern

  if (time_passed > 500)          // WENN vergangene Zeit seit letzter Ausführung größer 0,5 Sekunden ist
  {                               // >>
    lcd.setCursor(0,0);           // Ausgabe-Cursor des LCD auf Position 1, Zeile 1 setzen
    for (int i = 0; i < 20; i++)  // Cursor Positionen von Anfang bis Ende durchlaufen
    {                             // >>>
      lcd.write(line0[i]);        // Zeichen je angwählte Position Zeile 1 auf LCD ausgeben
    }                             // <<<
    lcd.setCursor(0,1);           // Ausgabe-Cursor des LCD auf Position 1, Zeile 2 setzen
    for (int i = 0; i < 20; i++)  // Cursor Positionen von Anfang bis Ende durchlaufen
    {                             // >>>
      lcd.write(line1[i]);        // Zeichen je angwählte Position Zeile 2 auf LCD ausgeben
    }                             // <<<
    lcd.setCursor(0,2);           // Ausgabe-Cursor des LCD auf Position 1, Zeile 3 setzen
    for (int i = 0; i < 20; i++)  // Cursor Positionen von Anfang bis Ende durchlaufen
    {                             // >>Y
      lcd.write(line2[i]);        // Zeichen je angwählte Position Zeile 3 auf LCD ausgeben
    }                             // <<<
    lcd.setCursor(0,3);           // Ausgabe-Cursor des LCD auf Position 1, Zeile 4 setzen
    for (int i = 0; i < 20; i++)  // Cursor Positionen von Anfang bis Ende durchlaufen
    {                             // >>>
      lcd.write(line3[i]);        // Zeichen je angwählte Position Zeile 4 auf LCD ausgeben
    }                             // <<<
    last_executed = millis();     // Setze letzte Ausführung über Variable "last_executed" auf aktuelle Laufzeit
  }                               // <<
}
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

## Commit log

2025-08-22 Add CAD-file for housing of electronics
    CAD-data-file (FreeCAD format) for the housing of the electronics including lower part and lid with cutouts / holes for cable inputs, display, switches.
    [Taupunkt_Lueftung_Gehaeuse.FCStd]
2025-08-22 Add housing lower part STEP file for 3D-printing
    STEP file for 3D-printing of housing lower part based on the CAD file
    [Taupunkt_Lueftung_Gehaeuse-Unterteil.step]
2025-08-22 Add housing lid STEP file for 3D-printing
    STEP file for 3D-printing of housing lid based on the CAD file
    [Taupunkt_Lueftung_Gehaeuse-Deckel.step]
2025-08-22 Update README.md
    Übersicht der verwendeten Software hinzugefügt
2026-04-02 Delete Taupunkt_Lueftung_Gehaeuse-Deckel.step
    Falsche Datei
    [Taupunkt_Lueftung_Gehaeuse-Deckel.step]
2026-04-02 Delete Taupunkt_Lueftung_Gehaeuse-Unterteil.step
    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
    [Taupunkt_Lueftung_Gehaeuse-Unterteil.step]
2026-04-02 Delete Taupunkt_Lueftung_Gehaeuse.FCStd
    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
    [Taupunkt_Lueftung_Gehaeuse.FCStd]
